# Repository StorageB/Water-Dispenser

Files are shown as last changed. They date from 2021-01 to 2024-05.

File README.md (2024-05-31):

## Automatic Filtered Water Dispenser

### Project Description 

This project is an for an electronic water dispenser connected to an under counter filtration system. The most current version includes the following features:

- Automatically dispenses water when a glass is placed under the tap using two short range infrared sensors
- Dispenses water when a button is pressed
- Logs water usage data to a Google Sheets document to keep track of daily and total water usage
- Bottle fill function
  - Press and hold button to select from a preset amount of water to dispense (16oz, 24oz, 32oz, etc.)
  - Purple LEDs flash to indicate which preset amount is being selected
  - Preset values are read from the Google Sheets document so they are easily adjustable
- Filter change alert
  - Red LEDs flash to indicate the filter needs to be changed
  - Total water usage is loaded from Google Sheets document
- Automatic LED dimming at night based on time of day scheduling entered in the Google Sheets document
- 3D printed enclosure for hidden mounting under a cabinet

### Project Information

* [wiring diagram](https://github.com/StorageB/Water-Dispenser/blob/master/img/wiring-diagram.jpeg)

* [parts list](https://github.com/StorageB/Water-Dispenser/blob/master/parts-list.md)

* [3D printed enclosure](https://github.com/StorageB/Water-Dispenser/blob/master/Enclosure.stl)

* [picture gallery](http://imgur.com/a/mHQLtMX)

### Code

There are three different versions of the code posted for the ESP8266:

1. [Version 1](https://github.com/StorageB/Water-Dispenser/blob/master/main_v1.cpp) - Basic Functionality 

   This includes the most basic operation for one sensor and can be used without an internet connection. It will open the valve and fade on the lights when an object is detected or when the button is pressed.

2. [Version 2](https://github.com/StorageB/Water-Dispenser/blob/master/main_v2.cpp) - Google Sheets logging

   This version has the same functionality as version 1, but includes code for over the air (OTA) programming of the ESP8266 and for logging water usage data directly to Google Sheets

3. [Version 3](https://github.com/StorageB/Water-Dispenser/blob/master/main_v3.cpp) - Current version 

   This is the most recent version, and includes the code for all of the features listed above in the Project Description.

### Build Notes and Considerations

#### Google Sheets Logging

Google sheets is used to log water usage data and for the system to read inputs such as when the filter should be changed, what preset values to use for the automatic dispensing mode, and for scheduling afterhours times.

A tutorial for how to log data to Google Sheets with an ESP8266 module without the use of a third party service can be found here:
https://github.com/StorageB/Google-Sheets-Logging

#### Controller

A NodeMCU controller was used mainly because a WiFi connection was required for logging data and for the desire to use over the air programming. 

#### Valve

1.  The water valve should be a fail close valve. If the power goes out or signal is otherwise lost from the microcontroller, the valve should close or remain closed.
2.  You can find cheaper solenoid valves on Amazon or other sites, but keep in mind the following when selecting a valve:
      - Safety: It needs to be safe to use for beverage applications (should use lead free brass and safe to drink from plastics). 
      - Reliability: This is a commercial valve made specifically for this application. I would not trust a $3 valve from Amazon when installing this permanently in my house.
3.  It is a good idea to have a delay after the valve is open before it is allowed to close. This will prevent rapid or partial switching of the valve that may lead to early failure.

#### IR Sensor

1. I chose infrared sensors over an ultrasonic sensor for this application for a few reasons. 
   - Simplicity: The sensor used simply outputs a low signal when an object is detected, and a high signal otherwise.
   - Size: The sensor is much smaller than an ultrasonic sensor module and will be easier to hide under the cabinet where it is mounted.
   - Health: There is a bit of research that suggests long term exposure to ultrasonic waves, although out of our hearing range, may have a negative impact on people. And since this will be running 24/7, I prefer using an IR sensor. Additionally, the frequency of an ultrasonic sensor module is in the hearing range of dogs.  
2. Sensor range: I chose a sensor with a short range of between 2 cm and 10 cm (0.8" and 4"). Because it is mounted above the kitchen sink, I did not want it to be accidentally triggered when using the sink.
3. Ghost Detection: Occasionally an IR sensor may give you false triggers based on what the light may be reflecting on (such as dust). I was having this problem but solved it but adding a simple 100 ms delay after it was triggered. After the delay, the system checks again to see if the sensor is still triggered. This also reduced rapid on/off switching of the valve if an object was just on the edge of detection.
4. IR sensors do not work well with glass. The sensors had to be positioned to detect a hand holding a glass. 
5. Code has been added for the valve to stay open for a short amount of time after an object is no longer detected. This help prevent the valve from rapidly opening and closing if the sensor is not continuously triggered when an object is on the edge of the detection zone of the sensor.

#### NeoPixel LED ring

Because the ESP module uses 3.3V for the GPIO pins, a level shifter was required for the 5V NeoPixel ring. Although you can get by without a level shifter for some applications, to do very quick changes such as fading all of the LEDs on/off the level shifter was required. Without it, the LEDs had unstable and erratic behavior.

Adafruit has an excellent guide for how to get started with NeoPixels: https://learn.adafruit.com/adafruit-neopixel-uberguide

#### Fading LEDs

When fading LEDs with PWM, the light output levels do not scale linearly. Therefore, a logarithm curve is required. This post gives a great explanation on this along with some example Arduino code that I used in this project: https://diarmuid.ie/blog/pwm-exponential-led-fading-on-arduino-or-other-platforms

#### Handling Malfunctions

I added code to shut off the valve in the case that it was open for an abnormally long amount of time. This could be the result of a faulty sensor, disconnected sensor signal wire, stuck switch, electrical short, blocked sensor, etc. In addition, the LEDs will display an error (flashing red), and the system will have to be manually reset before it is allowed to be used again.

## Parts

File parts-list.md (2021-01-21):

## Parts List

### Plumbing

| Item | Cost | Product Link |
| --- | ---- | :--- |
| water filtration system | $99  | [Aquasana](https://www.aquasana.com/drinking-water-filter-systems/under-counter-faucet-2-stage/chrome) |
| water tubing | $5 | [Home Depot](https://www.homedepot.com/p/Everbilt-1-4-in-O-D-x-1-6-in-I-D-x-25-ft-Polyethylene-Tubing-701873/207144363) |
| water fittings for valve (x2) | $10  | [Home Depot](https://www.homedepot.com/p/Everbilt-1-4-in-x-1-4-in-MIP-Lead-Free-Brass-Compression-Adapter-Fitting-801079/207176793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) |
| 90 degree tap fitting | $4 | [Home Depot](https://www.homedepot.com/p/John-Guest-1-4-in-O-D-x-1-4-in-O-D-NPTF-Polypropylene-Push-to-Connect-90-Degree-Elbow-Fitting-804529/303347813) |
| PTFE tape | $1 | [Home Depot](https://www.homedepot.com/p/Harvey-1-2-in-x-260-in-PTFE-Tape-0178502/202280370) |
| | | |

### Electronics

| Item | Cost | Product Link |
| --- | ---- | :--- |
| electric solenoid valve | $20  | [Electric Solenoid Valves](https://www.electricsolenoidvalves.com/1-4-12v-dc-electric-plastic-solenoid-valve/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) |
| ESP8266 dev board | $5 | [Amazon](https://www.amazon.com/HiLetgo-Internet-Development-Wireless-Micropython/dp/B010N1SPRK?ref_=ast_sto_dp) |
| N-Channel MOSFET | $1 | [Adafruit](https://www.adafruit.com/product/355) |
| IR sensor (x2) | $18  | [Adafruit](https://www.adafruit.com/product/1927) |
| LED ring (16 LEDs) | $10  | [Adafruit](https://www.adafruit.com/product/1463) |
| level shifter | $1 | [Adafruit](https://www.adafruit.com/product/1787) |
| buck converter module | $2 | [Amazon](https://www.amazon.com/Valefod-Efficiency-Voltage-Regulator-Converter/dp/B076H3XHXP?ref_=ast_bbp_dp&th=1&psc=1) |
| 12V power supply | n/a  | |
| | | |

### Notes

1. Many components were purchased from my local electronics store so links to products may not reflect where I actually bought the product.
4. The cost of the Aquasana filtration system fluctuates quite a bit. Watch for sales or promotions to get it for $99. 
3. Some items were purchased in bulk but the cost reflects only the items that were required for the project.
4. The cost for parts I scavenged from around the house were not included.

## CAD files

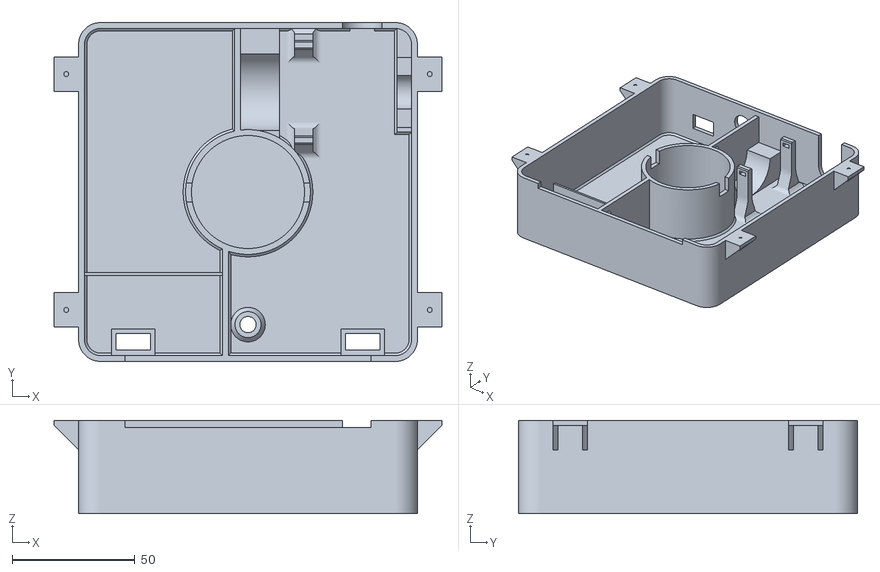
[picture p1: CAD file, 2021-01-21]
Enclosure.stl
158.0 x 138.0 x 38.0

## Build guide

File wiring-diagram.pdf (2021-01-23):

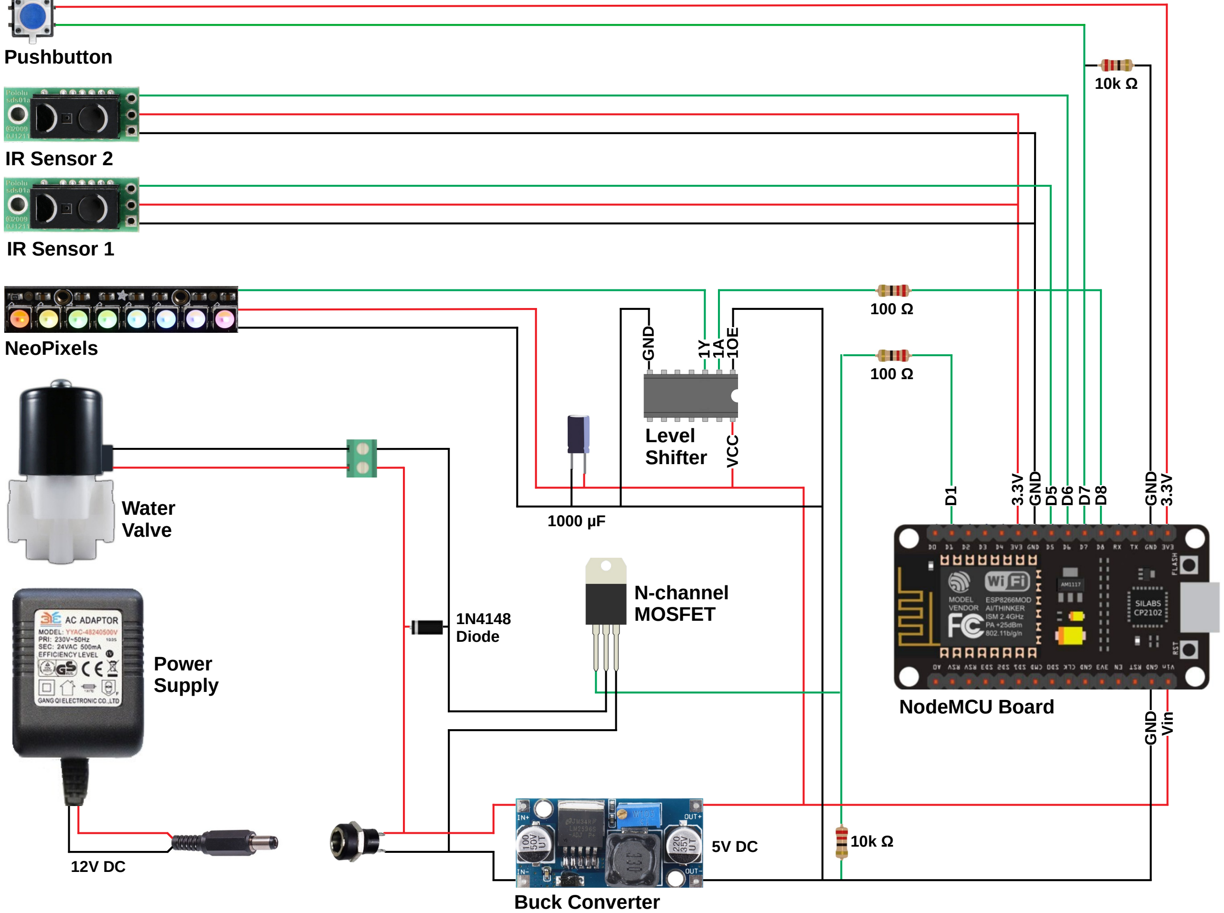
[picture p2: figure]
IR Sensor 2; N-channel MOSFET; Buck Converter; NeoPixels; Level Shifter; D Vin; Pushbutton; NodeMCU Board; IR Sensor 1; Water Valve; Power Supply; 1N4148 Diode

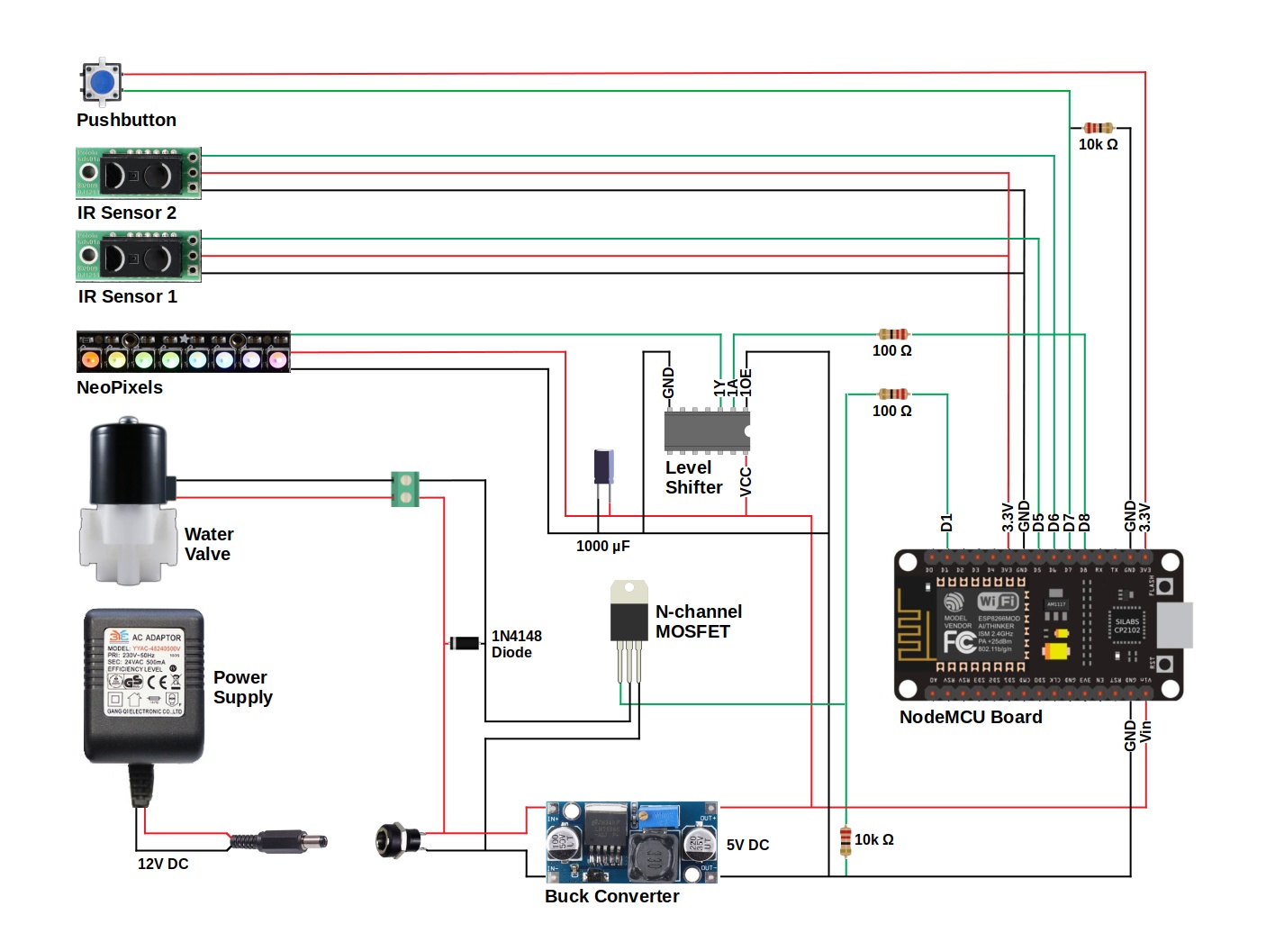
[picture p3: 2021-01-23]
img/wiring-diagram.jpeg

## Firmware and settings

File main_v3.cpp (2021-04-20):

//  ===========================================
//  Automatic Water Dispenser
//  https://github.com/StorageB/Water-Dispenser
//
    #define version_number "v3.2021-04-19-1112"
//  ===========================================


#include <Arduino.h>
#include <Adafruit_NeoPixel.h>
#include <ESP8266WiFi.h>
#include <ESP8266mDNS.h>
#include <WiFiUdp.h>
#include <ArduinoOTA.h>
#include <HTTPSRedirect.h>
#include <NTPClient.h>
#include <Wire.h>
#include <ArduinoJson.h>
#include <Timezone.h>

#define valve_output      D1          // valve output pin
#define ir1_input         D5          // ir 1 sensor input pin
#define ir2_input         D6          // ir 2 sensor input pin
#define switch1_input     D7          // pushbutton input pin
#define led_pin           D8          // NeoPixel ring signal pin

#define led_count         28          // number of LEDs in NeoPixel ring
#define pwm_intervals     20          // number of intervals in the fade in/out for loops for fading LEDs
#define ir_input_delay    100         // how long to wait once an IR sensor is triggered before opening valve (to prevent false triggers)
#define sw_input_delay    30          // how long to wait once switch is pressed before opening valve (debounce)
#define log_delay         240000      // amount of time to wait before publishing data to Google Sheets
#define display_off_delay 3000        // amount of time to wait once valve is closed before turning off the display LEDs
#define error_time        300000      // amount of time valve can be open before automatically turning off and displaying an error (protect against blocked or failed sensor, disconnected or shorted wiring, etc)
#define cycle_time        250         // amount of time valve must remain closed before reopening (allow valve to fully close before attempting to reopen and prevent rapid on/off switching of valve)
#define turn_off_delay    400         // amount of time to wait to turn off valve after sensor no longer detects an object
#define button_hold_time  850         // amount of time to hold button down before next button hold function (used to select different automatic dispense preset amounts: 16oz, 24oz, 32oz, etc.)
#define led_blink         700         // amount of time delay between flashing LEDs during auto dispense mode
#define time_check        300000      // how often to check the time from the NPT server
#define dim_factor        10          // factor by which to dim the LEDs during afterhours times

bool debug_mode = false;              // debug mode disables the valve from turning on and enables green lights when publishing (water usage data will still be calculated and published)
bool display_orange_led = false;      // ***NOTE: need to increase turn_off_delay to ~800 if this is true***     display orange LEDs in IR mode when object is out of sensor range when water is dispensing when set to true

int led_brightness = 255;             // NeoPixel brightness (max = 255)
int ir1_state;                        // state of IR sensor 1: LOW if object detected, HIGH if no object detected
int ir2_state;                        // state of IR sensor 2: LOW if object detected, HIGH if no object detected
int switch1_state;                    // state of pushbutton: HIGH if pressed, LOW if not pressed
int error_status = 0;                 // used to report an error, set to 0 if no errors
int current_hour = 12;                // current hour of the day (0 to 23) (value will be set from )
int total_gallons = 0;                // total gallons of water used  (default value set, but will import value from Google Sheets at startup and after publishing data)
int oz_target = 128;                  // total ounces daily target    (default value set, but will import value from Google Sheets at startup and after publishing data)
int filter_change = 500;              // what value to change filter  (default value set, but will import value from Google Sheets at startup and after publishing data)
int brightness;                       // used in the fade_in and fade_out loops to calculate and set LED brightness
int button_press_multiplier = 1;      // used to determine the next function when holding down the button
int function_1_oz = 0;                // automatic dispense ounces (default value set, but will import value from Google Sheets at startup and after publishing data)
int function_2_oz = 0;                // automatic dispense ounces (default value set, but will import value from Google Sheets at startup and after publishing data)
int function_3_oz = 0;                // automatic dispense ounces (default value set, but will import value from Google Sheets at startup and after publishing data)
int function_4_oz = 0;                // automatic dispense ounces (default value set, but will import value from Google Sheets at startup and after publishing data)
int function_5_oz = 0;                // automatic dispense ounces (default value set, but will import value from Google Sheets at startup and after publishing data)
int automatic_dispense_oz = 0;        // how much water to dispense automatically (based on which amount was selected when the button is held down)
int automatic_dispense_time = 0;      // calculated length of time to keep water on when automatically dispensing
int afterhours_start = -1;            // beginning hour of afterhours time (0 to 23, with 0 being midnight and 23 being 11pm, -1 to disable) (default value set, but will import value from Google Sheets at startup and after publishing data)
int afterhours_stop = -1;             // ending hour of afterhours time    (0 to 23, with 0 being midnight and 23 being 11pm, -1 to disable) (default value set, but will import value from Google Sheets at startup and after publishing data)

bool display_on = false;              // is the display on?
bool led_on = false;                  // is the LED ring on?
bool valve_open = false;              // is the valve open?
bool data_published = false;          // has current data been published? 
bool case_off = false;                // is the button function set to off? (the case when the button is held down long enough to cycle through all the preset functions and should now not dispense any water when button is released)
bool restart_clock = true;            // does the timer used to determine when to check the current time need to be restarted? (has time been checked?)
bool afterhours = false;              // used for afterhours settings (dim LEDs)
bool orange_led = false;              // used in fade_out function call if the fade out color should be orange (when using IR sensors) instead of blue (when using push button)

bool button_pressed = false;          // mode of operation: button pressed
bool auto_dispense = false;           // mode of operation: button pressed and held down for automatic operation using a timer
bool sensor_triggered = false;        // mode of operation: IR sensor

unsigned long current_time = 0;       // used to get the current time
unsigned long timer_start = 0;        // used to start timer to keep track of how long the valve is open
unsigned long run_time = 0;           // used to calculate how long the valve was open
unsigned long run_total = 0;          // used to keep track of total run time before publishing time
unsigned long log_timer = 0;          // used to determine when to publish data
unsigned long clock_timer = 0;        // used to determine when to check the current time
unsigned long display_timer = 0;      // used to determine when to turn off the display LEDs
unsigned long turn_off_timer = 0;     // used to determine when to turn off the value when the IR sensors are no longer triggered 
unsigned long blink_time = 0;         // used to determine when to blink the LED during auto dispense mode
unsigned long button_press_time = 0;  // used to determine when the button was pressed

float conversion_factor = 0.0000;     // gallons per second conversion factor (default value set, but will update from Google Sheets at startup and after publishing data)
float R = (pwm_intervals * log10(2))/(log10(255));  // used to calculate the 'R' value for fading LEDs


// Enter network credentials
#ifndef STASSID
#define STASSID "network"
#define STAPSK  "password"
#endif
const char* ssid = STASSID;
const char* password = STAPSK;

// Enter Google Script ID here
const char *GScriptId = "enter_google_script_id_here"";
#define gs_version_number "Version 48" // the version of the Google Scripts deployment listed above (not required, only for printing out version number at boot)

// Enter command and Google Sheets sheet name here
String payload_base =  "{\"command\": \"insert_row\", \"sheet_name\": \"Sheet1\", \"values\": ";
String payload = "";

// Information for reading and writing to Google Sheets (do not edit)
const char* host = "script.google.com";
const int httpsPort = 443;
const char* fingerprint = "";
String url = String("/macros/s/") + GScriptId + "/exec?cal";
String return_string = "";

// Define HTTPSRedirect client
HTTPSRedirect* client = nullptr;

// US Central Time Zone (Chicago, IL)
TimeChangeRule myDST = {"CDT", Second, Sun, Mar, 2, -300}; // Daylight time = UTC - 5 hours
TimeChangeRule mySTD = {"CST", First, Sun, Nov, 2, -360};  // Standard time = UTC - 6 hours
Timezone myTZ(myDST, mySTD);
TimeChangeRule *tcr; // pointer to the time change rule, use to get TZ abbrev

// Declare NeoPixel strip object
Adafruit_NeoPixel strip(led_count, led_pin, NEO_GRB + NEO_KHZ800);


// Function to return the compile date and time as a time_t value
time_t compileTime()
{
    const time_t FUDGE(10); // fudge factor to allow for compile time (seconds, YMMV)
    const char *compDate = __DATE__, *compTime = __TIME__, *months = "JanFebMarAprMayJunJulAugSepOctNovDec";
    char chMon[4], *m;
    tmElements_t tm;

    strncpy(chMon, compDate, 3);
    chMon[3] = '\0';
    m = strstr(months, chMon);
    tm.Month = ((m - months) / 3 + 1);

    tm.Day = atoi(compDate + 4);
    tm.Year = atoi(compDate + 7) - 1970;
    tm.Hour = atoi(compTime);
    
    tm.Minute = atoi(compTime + 3);
    tm.Second = atoi(compTime + 6);
    time_t t = makeTime(tm);
    return t + FUDGE; // add fudge factor to allow for compile time
}
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
void loop() {
  ArduinoOTA.handle(); // required for OTA programming

  // Publish data to Google Sheets
  if (!valve_open && !display_on && !data_published) {
    publish_data();
  }

  // Read status of sensors and pushbutton
  ir1_state = digitalRead(ir1_input);         // get status of IR sensor 1
  ir2_state = digitalRead(ir2_input);         // get status of IR sensor 2
  switch1_state = digitalRead(switch1_input); // get status of pushbutton
  

  // Button has been pressed (press on, press off, hold down for automatic dispense functions)
  if (switch1_state == HIGH && !sensor_triggered) {
    delay(sw_input_delay);
    switch1_state = digitalRead(switch1_input);
    if (switch1_state == HIGH) {
      if (!valve_open) {
        button_pressed = true;
        button_press_time = millis();
        
        while (!valve_open && switch1_state == HIGH) { // enter while loop if button is still pressed
          switch1_state = digitalRead(switch1_input);  // check if button still held down
          current_time = millis();
          if (current_time - button_press_time > (button_hold_time * button_press_multiplier)) { // execute the cases below when button has been held down for correct amount of time (ex: case 1 executed when button held down for 1 second, case 2 at 2 seconds, etc.)
            if (function_1_oz != 0) { // only run automatic dispense function if data has been imported from google sheets, otherwise auto shut off won't work as the function_x_oz variables will all still be set to zero
              switch (button_press_multiplier) {
                case 1:
                  Serial.print("Function 1: ");
                  Serial.print(function_1_oz);
                  Serial.println("oz");
                  auto_dispense = true;
                  fade_in("purple", 7);
                  fade_out("purple", 7);
                  automatic_dispense_oz = function_1_oz;
                  button_press_multiplier ++;
                  break;
                case 2:                  
                  Serial.print("Function 2: ");
                  Serial.print(function_2_oz);
                  Serial.println("oz");
                  auto_dispense = true;
                  fade_in("purple", 7);
                  fade_out("purple", 7);
                  automatic_dispense_oz = function_2_oz;
                  button_press_multiplier ++;
                  break;
                case 3:                    
                  Serial.print("Function 3: ");
                  Serial.print(function_3_oz);
                  Serial.println("oz");
                  auto_dispense = true;
                  fade_in("purple", 7);
                  fade_out("purple", 7);
                  automatic_dispense_oz = function_3_oz;
                  button_press_multiplier ++;
                  break;
                case 4:                
                  Serial.print("Function 4: ");
                  Serial.print(function_4_oz);
                  Serial.println("oz");
                  auto_dispense = true;
                  fade_in("purple", 7);
                  fade_out("purple", 7);
                  automatic_dispense_oz = function_4_oz;
                  button_press_multiplier ++;
                  break;    
                case 5:      
                  Serial.print("Function 5: ");
                  Serial.print(function_5_oz);
                  Serial.println("oz");
                  auto_dispense = true;
                  fade_in("purple", 7);
                  fade_out("purple", 7);
                  automatic_dispense_oz = function_5_oz;
                  button_press_multiplier ++;
                  break;   
                case 6:
                  Serial.println("Function 6: Off");
                  auto_dispense = false;
                  case_off = true;
                  button_press_multiplier ++;
                  break;
                case 7:
                  Serial.println("Function 7: empty");            
                  button_press_multiplier ++;
                  break;
                case 8:
                  Serial.println("Function 8: publish/retrieve data");
                  fade_in("green", 5);
                  log_timer = log_delay + 1; // set the log timer greater than the log delay
                  publish_data();
                  fade_out("green", 5);
                  log_timer = millis(); // reset the log timer                     
                  button_press_multiplier ++;
                  break;                              
                default: // default case if none of the above cases match
                  break;
              }
            }
            else{ // publish data if the button has been held down but data has not yet been imported from Google Sheets
              fade_in("green", 5);
              case_off = true;
              log_timer = log_delay + 1; // set the log timer greater than the log delay
              publish_data();
              fade_out("green", 5);
              log_timer = millis(); // reset the log timer
            }
          }
          yield(); // required to keep from crashing in while loop
        } // end while
        
        // when button is released, turn on water unless button was held down to the 'off' function 
        if (case_off) { 
          button_pressed = false;
          button_press_multiplier = 1;
          Serial.println("automatic dispense off");
          case_off = false;
        }
        else {
          turn_on();  
        }
        
        // if automatically dispensing, calculate how long to leave water on
        if (auto_dispense) {
          automatic_dispense_time = automatic_dispense_oz / (conversion_factor * 0.001 * 128); 
          Serial.print("automatically dispensing ");
          Serial.print(automatic_dispense_oz);
          Serial.print("oz (");
          Serial.print(automatic_dispense_time);
          Serial.println("ms)");
        }

      }
      else if (valve_open) {  
        turn_off();
      }
    }
  } // end of button press
  

  // If automatically dispensing, turn valve off automatically based on calculated dispense time
  if (valve_open && auto_dispense) {
    current_time = millis();
    if (current_time - timer_start > automatic_dispense_time) {
      turn_off();
    }
  }


  // If button pressed, check for error if valve has been left open too long (if pressed and forgotten about)
  if (valve_open && button_pressed) {
    current_time = millis();
    if (auto_dispense) { // if automatically dispensing, flash LEDs instead of LEDs being solid on to indicate automatic dispense mode is activated
      if (current_time - blink_time > led_blink) {
        digitalWrite(LED_BUILTIN, !digitalRead(LED_BUILTIN));
        if (led_on) {fade_out("blue", 1); } else { fade_in("blue", 1);}
        blink_time = current_time;
      }
    }
  }


  // IR sensor has been triggered
  if ((ir1_state == LOW || ir2_state == LOW) && !button_pressed) {
    if (display_orange_led){ // if displaying orange LEDs when object is out of sensor range, this is required to turn LEDs blue when back in range
      if (led_on) {
        for(int j = 0; j < strip.numPixels(); j++) {
          if (!afterhours) {strip.setPixelColor(j,0,0,led_brightness);}
          if (afterhours)  {strip.setPixelColor(j,0,0,led_brightness/dim_factor);}
        }
        strip.show();
      }
    }
    if (!sensor_triggered) { // only delay if the water isn't on yet (prevent false triggers), no need for delay once water is on as that is handled by turn_off_delay
      delay(ir_input_delay);
      ir1_state = digitalRead(ir1_input);
      ir2_state = digitalRead(ir2_input);      
    }
    if (ir1_state == LOW || ir2_state == LOW) {
      turn_on();
      turn_off_timer = millis();
      sensor_triggered = true;
      if(display_orange_led) {orange_led = true;}
    }    
  }


  // Turn off water when in IR sensor mode
  if (sensor_triggered && (ir1_state == HIGH && ir2_state == HIGH)) {
    if(display_orange_led){ // display orange LEDs if object out of sensor range when water is on
      for(int j = 0; j < strip.numPixels(); j++) {
        if (!afterhours) {strip.setPixelColor(j,  led_brightness*0.75,              led_brightness*0.25,             0);}
        if (afterhours)  {strip.setPixelColor(j, (led_brightness/dim_factor)*0.75, (led_brightness/dim_factor)*0.25, 0);}
      }    
      strip.show();
    }
    current_time = millis();
    if (current_time - turn_off_timer > turn_off_delay) {
      turn_off();
    }
  }
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
